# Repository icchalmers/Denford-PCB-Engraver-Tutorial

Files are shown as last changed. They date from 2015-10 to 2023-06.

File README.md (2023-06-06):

# Denford PCB Engraver Tutorial

This tutorial will lead you through using the [Denford PCB Engraver](https://denford.co.uk/products/pcb-engraver/) to mill a small breakout board for a surface mount ATtiny85. The tutorial was written specifically for the FabLab at the University of Strathclyde, but should be applicable to anyone with a Denford PCB Engraver.

The best way to use the tutorial is in the browser. You can start at the beginning my going to the [Introduction](doc/introduction.md) or use the [Index](doc/index.md) to jump straight to a specific section.

The [latest release](https://github.com/icchalmers/Denford-PCB-Engraver-Tutorial/releases/latest) of the tutorial includes all of the example files and also has a PDF version that is easier for printing.

# Author

This tutorial was written by [Iain Chalmers](https://www.linkedin.com/in/iain-chalmers-0394753b). Any feedback is greatly appreciated and can be submitted by [opening an issue](https://github.com/icchalmers/Denford-PCB-Engraver-Tutorial/issues/new) on GitHub.

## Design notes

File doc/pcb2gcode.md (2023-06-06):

# Turning Gerbers Into GCode

To turn our gerber files into GCode that can be used to drive the engraver, we're going to use [pcb2gcode](https://github.com/pcb2gcode/pcb2gcode) with its graphical wrapper [pcb2gcodeGUI](https://github.com/pcb2gcode/pcb2gcodeGUI). In the FabLab@Strathclyde, this should be installed on Laptop 1 in `C:\pcb2gcode`.

When your first open the program, you need to import the settings for the Denford. To do this, go to `File->Load configuration file` and choose the [Denford_pcb2gcode.settings](/Denford_pcb2gcode.settings) file included with this tutorial. Note that this assumes you are using a 0.2 mm, 60° mill for the traces and a 2 mm corncob mill for the board outline. See the [Drill](./pcb2gcode.md#drill) section below for how to change these settings.

In the `Input/output` tab, select the gerbers you generated in the previous step. If you used the default KiCAD naming, your `Front` will be the file that ends in `-F_Cu.gbr`, `Outline` will be the file that ends in `-Edge_Cuts.gbr` and the `Drill` file will end in `.drl`.

One you have these files selected you should get a preview of the PCB as shown below.

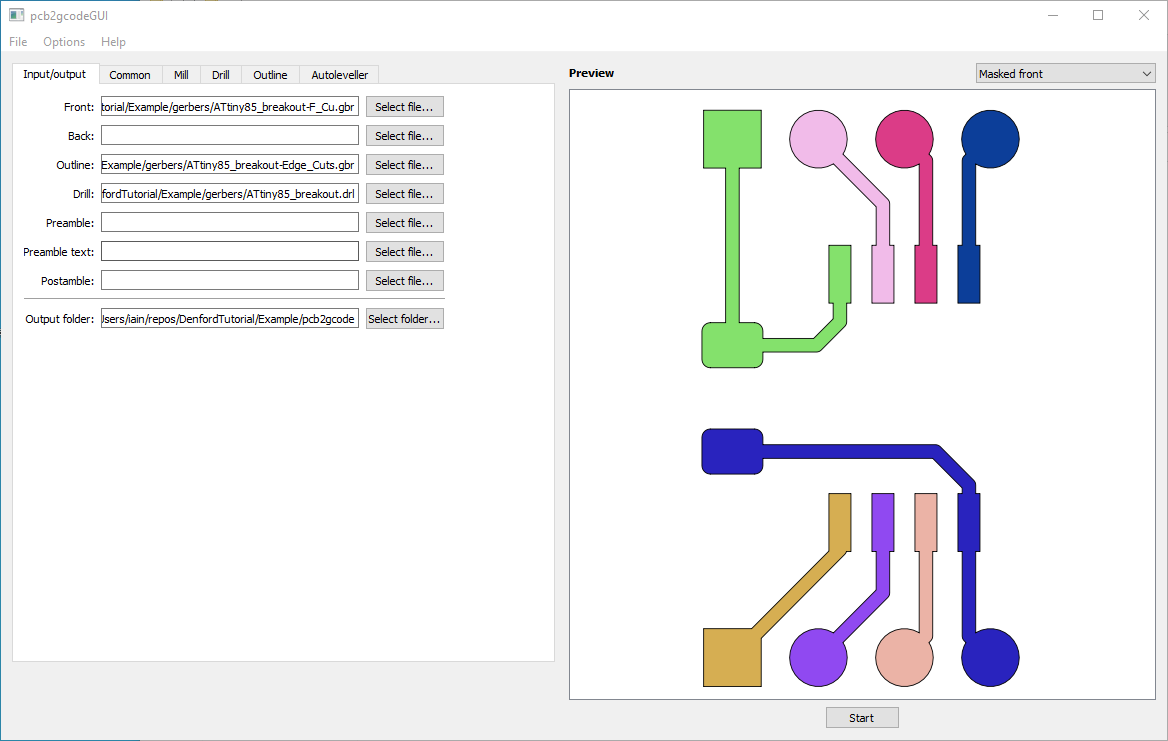
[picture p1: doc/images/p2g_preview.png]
p2g_preview


Once you choose a directory for the output files, you should just be able to hit `Start`. Assuming your design doesn't have any problems, you should see output similar to the below.

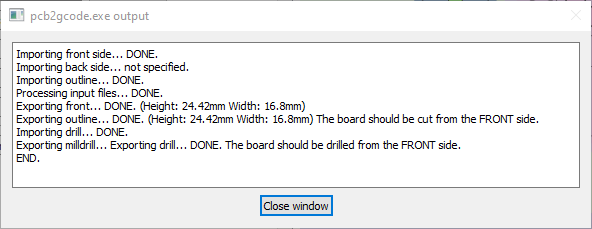
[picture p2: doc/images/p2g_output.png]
p2g_output


The preview window will now update to show the processed front. If there were any problems in the output generation, the preview can help you identify them. Note that where there is insufficient clearance between traces, pcb2gcdoe will default to trying to mill between the traces. This can lead to your traces being too thin, so it's better to fix problems in the design.

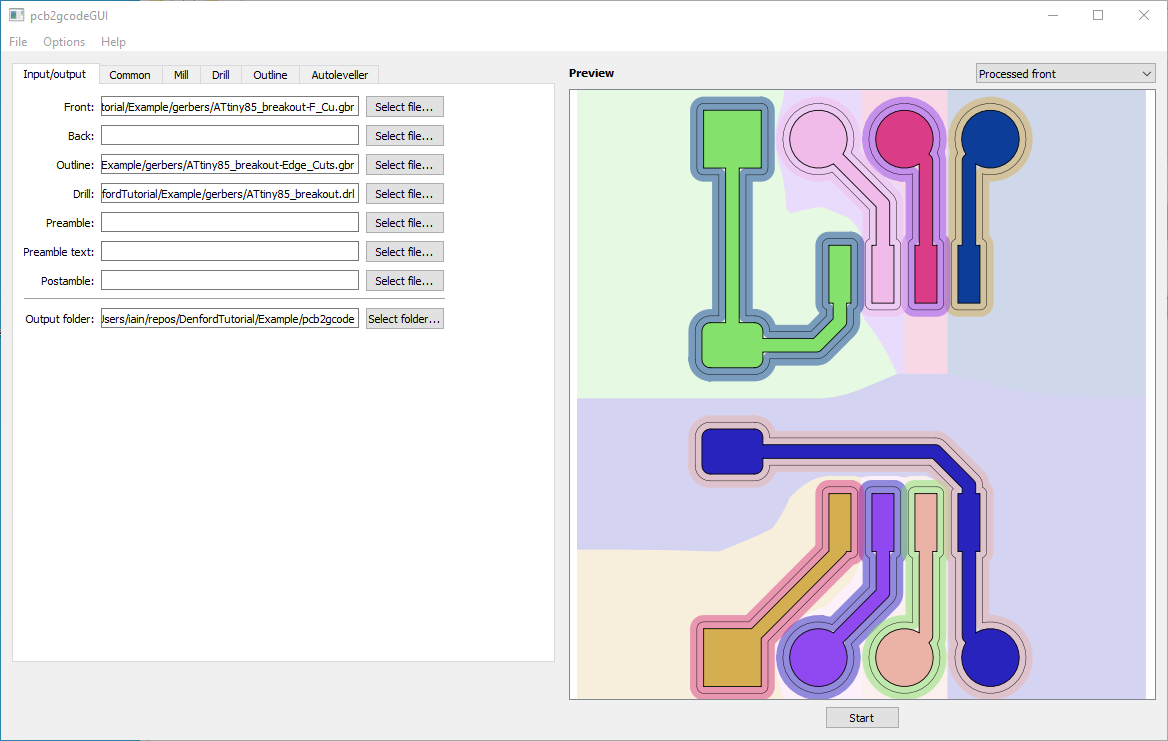
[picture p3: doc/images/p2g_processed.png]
p2g_processed


The output directory should now have a list of files similar to the one shown below. The three files we are most insterested in are the `.ngc` files, as these contain the GCode we will use to drive the Denford.

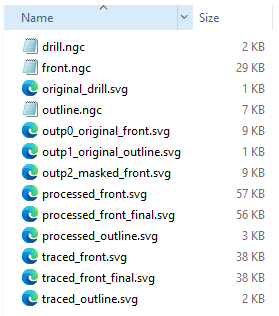
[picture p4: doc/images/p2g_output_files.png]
p2g_output_files


## Manual pcb2gcode Settings

### Common

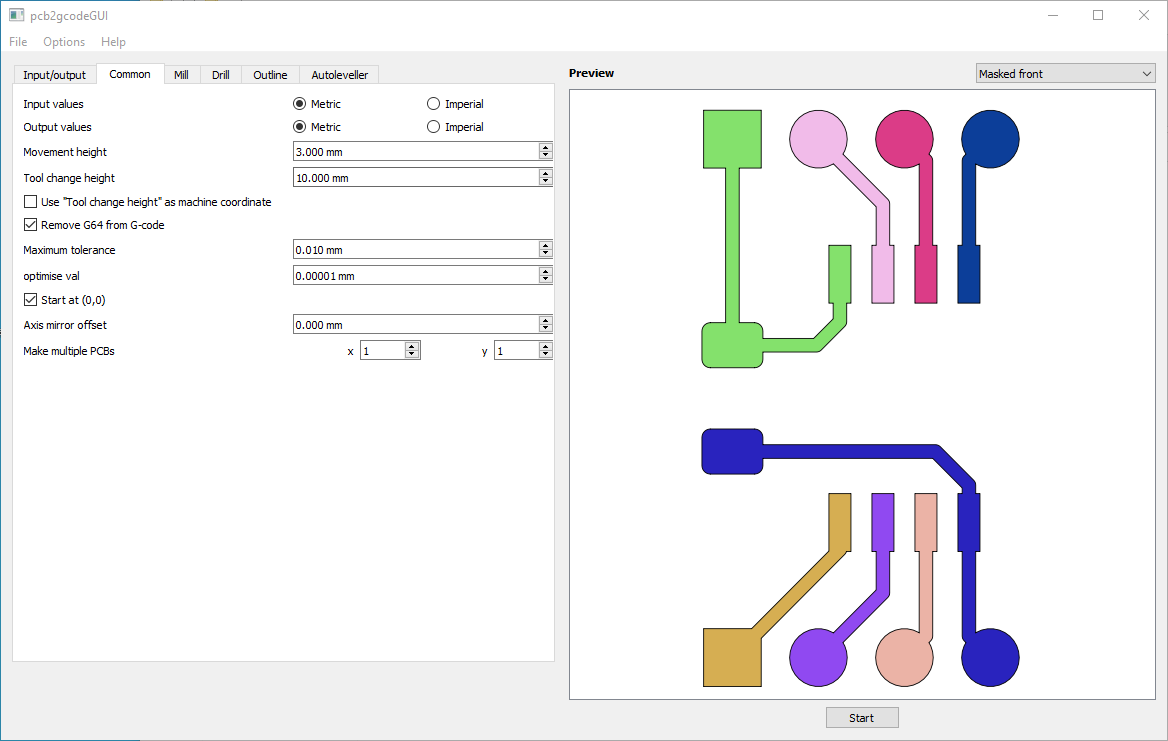
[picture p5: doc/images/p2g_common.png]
p2g_common


### Mill

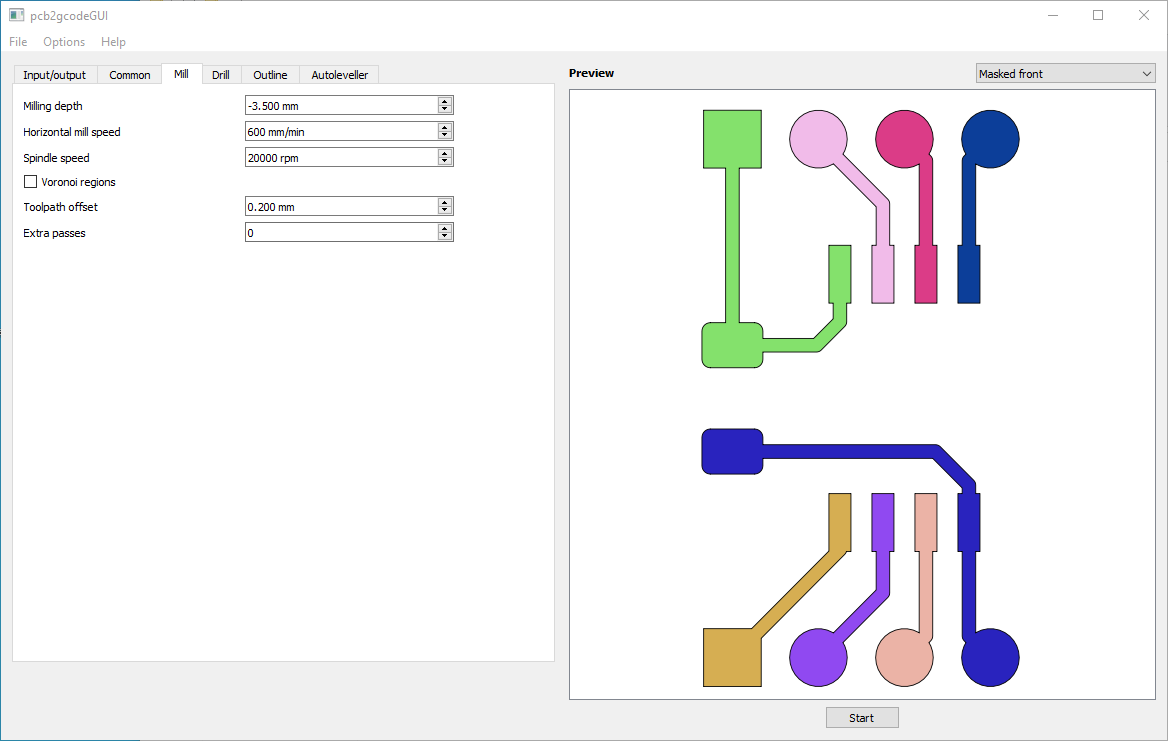
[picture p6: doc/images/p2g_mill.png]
p2g_mill


### Drill

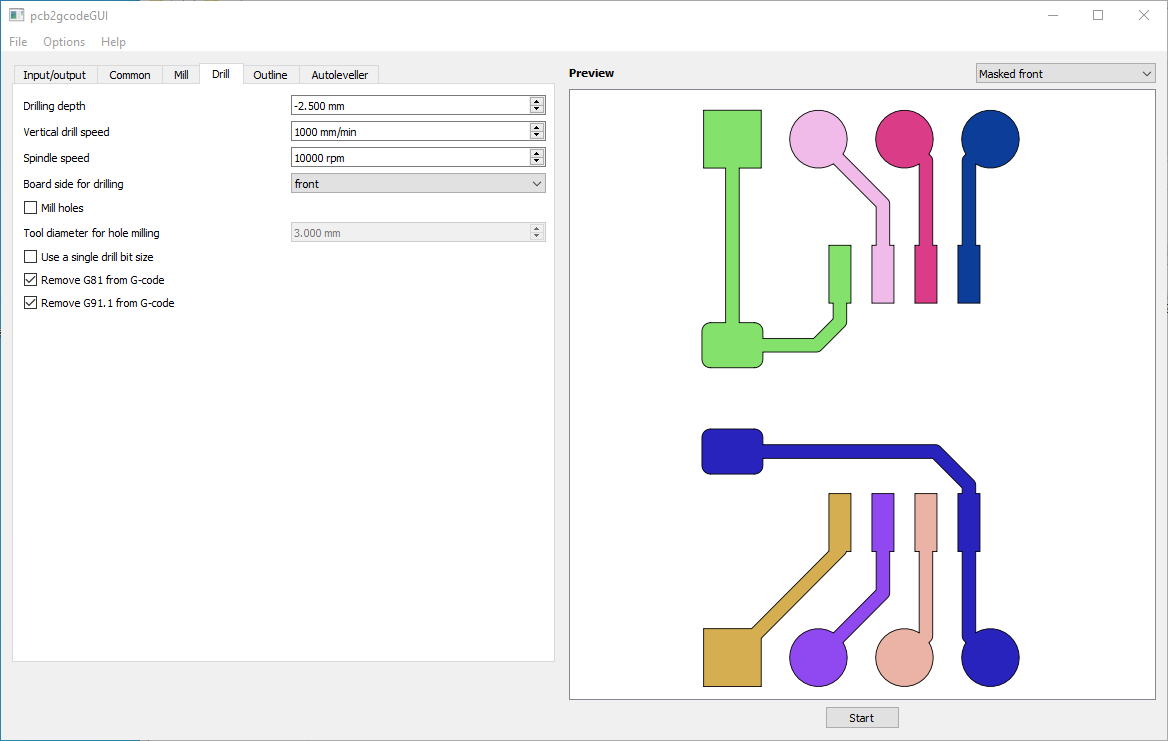
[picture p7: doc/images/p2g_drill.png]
p2g_drill


### Outline

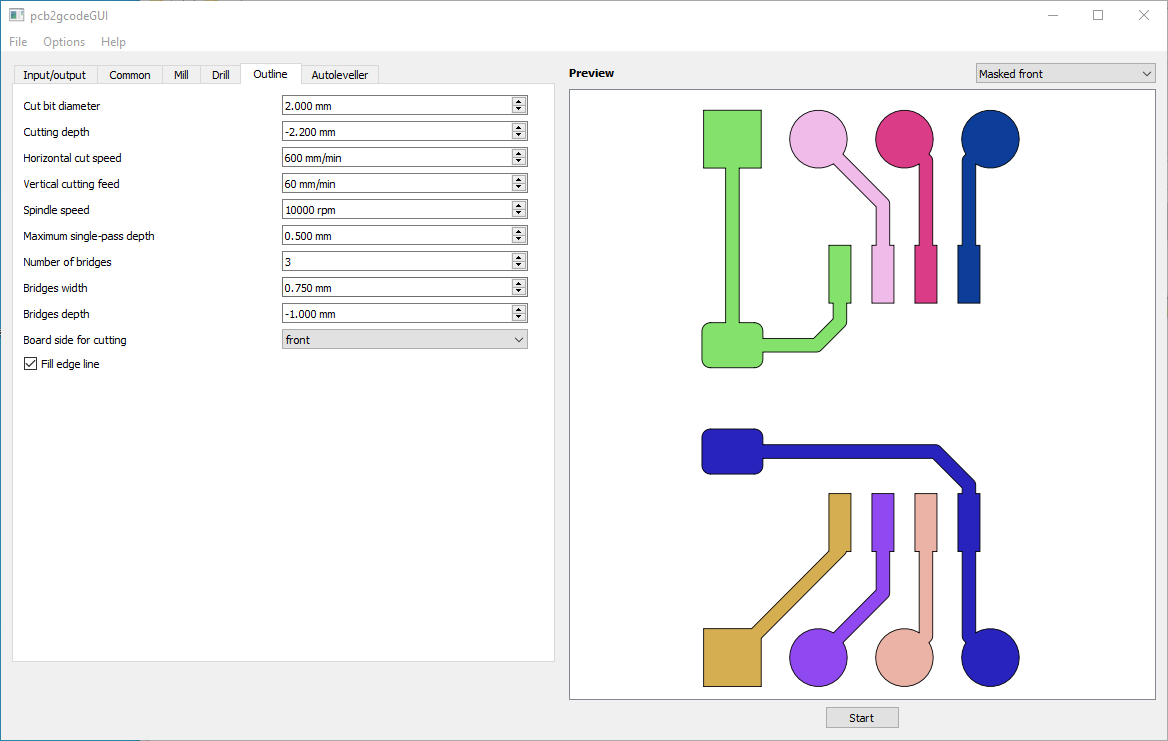
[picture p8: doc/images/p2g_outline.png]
p2g_outline


___
  <[Previous](kicadgerbers.md) | [Index](index.md) | [Next](milling.md)>

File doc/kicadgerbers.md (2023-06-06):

# Generating Gerbers Using KiCAD

In this tutorial, we're going to make a simple breakout board for an ATtiny85. You can find the KiCAD project [here](/example/PCB/).

If you want to skip this step because you don't have KiCAD installed, you can find the generated gerbers files [here](/example/gerbers/).

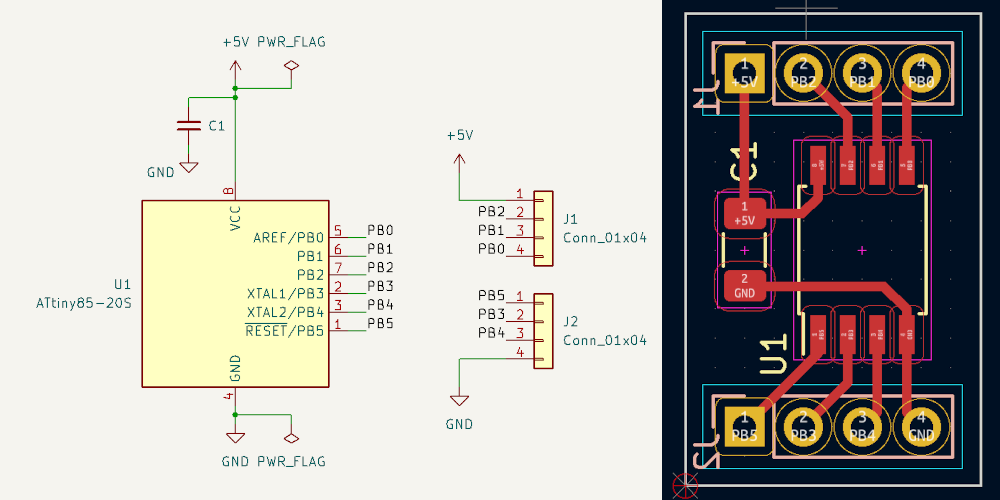
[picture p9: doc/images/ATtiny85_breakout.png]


If you're using different PCB design software, you can probably adapt the settings below for your software. If you want to contribute settings for your software, pull requests are welcome!

## DRC Constraints

Below are the DRC rules we recommend for projects designed to be made on the Denford. If you're using your own design, you can import the design rules from the example project to save yourself some time.

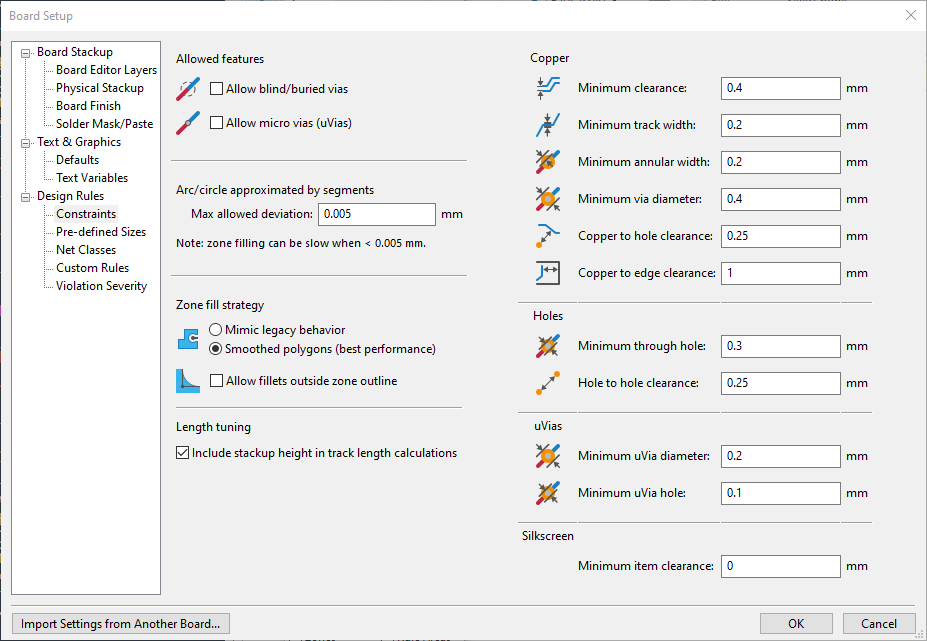
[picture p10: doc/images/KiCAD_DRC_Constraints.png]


## Gerber Generation Settings

Below are the recommended gerber generation settings for gettings gerbers compatible with pcb2gcode. Remember to set a sensible drill/place origin in your design.

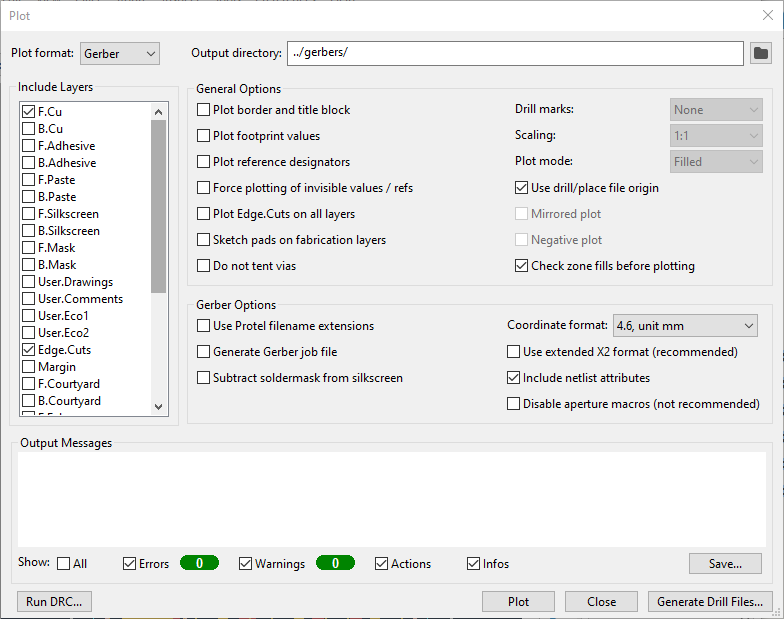
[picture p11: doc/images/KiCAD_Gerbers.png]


For the drill file, it's best to combine all of the drill hits into one file (as we can't do plated through holes anyway).

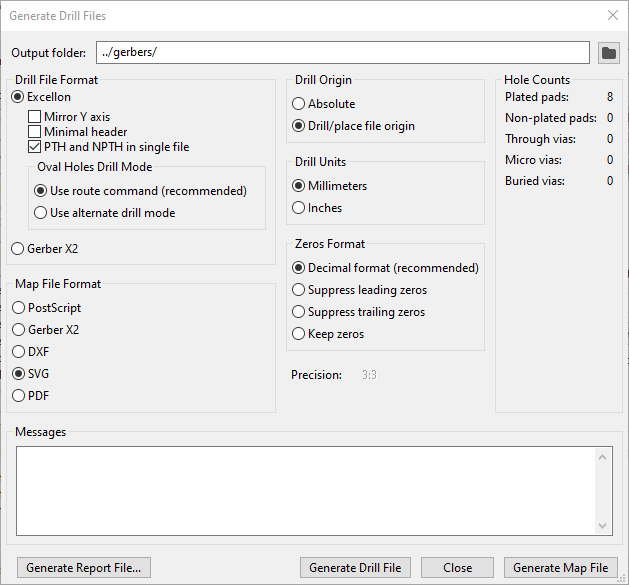
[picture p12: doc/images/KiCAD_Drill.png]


Once your gerber files are generated, you should have a set of files similar to the example ones [here](/example/gerbers/). The next step is to use pcb2gcode to convert our gerber files into GCode that we can use to drive the Denford.
___
  <[Previous](denfordengraver.md) | [Index](index.md) | [Next](pcb2gcode.md)>

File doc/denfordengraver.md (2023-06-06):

# Denford PCB Engraver

## Overview

You can find the full specification for the engraver on the [Denford website](https://denford.co.uk/products/pcb-engraver/). For our purposes, only two of the features are worth discussing:

- The maximum board size is 360 mm x 210 mm.
- The Z axis (that is, the bit that goes up and down) "floats" on top of the workpiece. The big advantage this brings over a traditional CNC is that the depth of cut into the copper (which is only 0.035 mm think) doesn't rely so heavily on the workpiece being completely flat with respect to the machine. That means it's easier to setup and V-shaped cutting bits give more consistent cut widths.

## Capabilities

In the FabLab@Stratchlyde, we use a combination of V-shaped milling bits for milling trace outlines and corncob bits for milling the PCB contour. If you use different bits, you might have slightly different capabilities but the list below should give you a decent idea of what the machine can do.

- **Single Sided PCBs:** While it is possible to engrave double-sided PCBs, it's almost always more hassle than it's worth. You would be surprised how complex a board you can get with just a single layer PCB. What I would call 1.5 layer PCBs are also easy - single layer boards where you add either 0 ohm resistors or a flying wire to jump signals where you need them. If you're feeling masochistic, you can see an example of a double-sided PCB [here](http://fabacademy.org/archives/2015/eu/students/chalmers.iain/week-11-outputs.html).
- **0.4 mm space:** We typically use [0.2 mm, 60° V-bit engraving bits](https://www.shop-apt.co.uk/carbide-engraving-tools-flat-bottom-half-round-60/3-175mm-1-8-diameter-carbide-engraving-cutter-0-2mm-tip-half-round-60.html). By the time these are cutting through the copper we find that they have a cut width of about 0.4 mm. We do have a combination of 0.1/0.2 mm and 30/60° bits, but the 0.2@60° bits are a good compromise between detail and bit life. Smaller spaces are possible with the 0.1 mm 30° bits but they are very fragile.
- **0.4 mm trace:** The hard limit on trace width is actually a fair bit smaller than 0.4 mm (limited by how small you can go before the trace gets lifted in the milling process). From experience, we've found that 0.4 mm for trace/space is a nice combination as it makes it easier to identify when the bits are wearing out, and at that combination you can still sneak a trace between the pads on 1206 (3216M) SMD parts.
- **Contour milling:** This was one of the main drivers to ditch the Denford software for generating the GCode, as it didn't support milling board outlines. pcb2gcode supports complex board outlines and automatically handles things like multi-pass cuts and bridge tabs. We use [2 mm corncob bits](https://www.aliexpress.com/item/32677591025.html?) because they're cheap and pretty hard to break. They don't give the cleanest of cut though, so it's best to keep traces at least 1 mm away from the edge of the PCB. We've experimented with some [2mm endmills](https://uk.rs-online.com/web/p/end-mills/6666681) that gave an excellent finish, but they're not really designed to plunge so required some extra steps to use. Plus, they're a lot more expensive.
- **Drill sizes:** The only sure way to know what drill sizes we have available is to check the box, but 0.5/0.8/1.0 mm are typically safe bets. We do have a range from 0.3 mm to 3 mm but it depends who's broken what recently! Generally it's best to limit yourself to as few drill sizes as possible so you don't have to change the bit a million times. I personally find you can bodge most drill hits to 0.5 mm for through hole components, 1 mm for headers and 3 mm for mounting holes.

## Limitations

Aside from the above, there are a few specific limitations that are worth keeping in mind:

- **FR1/FR2 substrates:** This is the copper clad material we mill the PCB from. We only allow the use of FR1 or FR2 substrates on the engraver.
  - FR1 is ideal as it is easy to mill. The downside is that it's a nightmare to source in small quantities at a reasonable price. We also found that it wasn't suitable to use in the reflow oven as the substrate tended to start to burn.
  - FR2 is a bit tougher on the bits but more widely available. Most of the PCB blanks we have in the FabLab@Strathclyde are FR2
  - FR4 is **not allowed** to be used in the engraver. Not only is the dust toxic, but FR4 is much harder than FR1/FR2 and it significantly reduces the life of the milling bits.

  To enforce this, **only materials purchased from the FabLab can be used on the engraver.** The main downside of FR2 is that it isn't capable of handling as high temperatures as FR4. It is possible to use it in the reflow oven, but it doesn't leave the best finish.
- **No solder mask:** Solder mask is the green stuff on top of almost every PCB you see. It protects the raw copper and also helps during soldering by forcing the solder to go where it's meant to. Without a solder mask, you can still use the reflow oven but it has a tendency to heavily discolour the copper to the point it looks burnt.
- **No silkscreen:** The lack of silkscreen can be unexpectedly annoying when it comes to populating your PCB!

## When To Use The Denford PCB Engraver

Keeping in mind the above capabilites and limitations, here's some advice on when the Denford PCB Engraver is a good choice for making your PCB:

- Simple quick'n'dirty prototypes. If you just need to prove out an idea, you can iterate on multiple designs in a day.
- If you need a breakout board for an IC because you forgot to order adapters.
- For one-off designs. For example, if you need to get a bunch of LEDs in the right place in a 3D model and you need a weird PCB shape to make it work.

I wouldn't recommend the engraver if:

- You want multiple copies of a finalised design.
- You want a long term, high quality PCB.
- Your design isn't simple enough to be implemented on a single layer PCB. The more complex a PCB (in terms of size, part and trace count), the more likely you are to run into issues producing it.

Once you're happy that your design is compatible with the engraver, it's time to generate the gerber files.
___
  <[Previous](introduction.md) | [Index](index.md) | [Next](kicadgerbers.md)>

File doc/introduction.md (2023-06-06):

# Introduction

This tutorial will lead you through using the [Denford PCB Engraver](https://denford.co.uk/products/pcb-engraver/) to mill a small breakout board for a surface mount ATtiny85. The tutorial was written specifically for the FabLab at the University of Strathclyde, but should be applicable to anyone with a Denford PCB Engraver.

If you are in the FabLab@Strathclyde, you should use this tutorial as a supplement to your machine induction.

All the files for this tutorial can be found on github: <https://github.com/icchalmers/Denford-PCB-Engraver-Tutorial>

Any feedback is greatly appreciated and can be submitted by [opening an issue](https://github.com/icchalmers/Denford-PCB-Engraver-Tutorial/issues/new) on GitHub.

## Prerequisites

This tutorial assumes you already know how to design a PCB in your CAD software of choice and generate gerber files for fabrication. The tutorial does cover how to generate gerbers suitable for the engraver using KiCAD, but the general settings should be easy enough to translate to other software (Eagle, Altium etc).

If you don't know how to design a PCB yet, I would recommend looking at [KiCAD](https://www.kicad.org/). Here are a few recommended resources to get your started:

- The KiCAD website has a (small) list of [recommended resources](https://www.kicad.org/help/learning-resources/).
  - In particular, see the offical KiCAD [Getting Started](https://docs.kicad.org/#_getting_started) guide.
- Chris Gammel of [Contextual Electronics](https://contextualelectronics.com/) has two excellent free course that teach you how to design a simple PCB:
  - [Shine On You Crazy KiCAD](https://contextualelectronics.com/courses/shine-on-you-crazy-kicad/)
  - [Getting to Blinky 5.0](https://contextualelectronics.com/courses/getting-to-blinky-5-0/)

## Software

To produce our PCB we'll be using two main pieces of software:

- [Denford PCB Engraver V1.9](https://denford.co.uk/software-downloads-support/): Although this is available for download on the Denford website, it needs a licence to work. It is only used for controlling the engraver, so you can still prepare all your files without it. If you're in the FabLab@Strathclyde, it should already be installed on Laptop 1.
Technically, the Denford software is capable of generating the milling files from gerbers directly, but it's very buggy and lacks some key features.
- [pcb2gcode](https://github.com/pcb2gcode/pcb2gcode): This is the software we use to turn gerbers into gcode that can be used on the engraver. Technically, we're using two bits of software. pcb2gcode is a command line only piece of software for turning gerber files into gcode for milling. We'll also be using the [pcb2gcodeGUI](https://github.com/pcb2gcode/pcb2gcodeGUI) wrapper to add a more user friendly interface and visualise the output. If you're in the FabLab@Strathclyde, it should be installed on Laptop 1. If there is no shortcut on the desktop, you can find it in `C:\pcb2gcode`.
  - When writing this tutorial I used pcb2gcode v2.5.0 and pcb2gcodeGUI v1.3.2-1. Installing these on Linux is pretty easy, but for Windows it can be a bit of a nightmare. I've included pre-compiled x64 Windows binaries in the [releases](https://github.com/icchalmers/Denford-PCB-Engraver-Tutorial/releases/latest) of this tutorial. See the readme in the release for installation help.
- [KiCAD](https://www.kicad.org/) (optional): I use KiCAD as my PCB design software and this tutorial will cover generating gerber files suitable for the engraver using KiCAD, but you can skip this if you already have gerbers ready to use. The [example PCB](/example/PCB/) was created in KiCAD V6.0.

Before we get started, we'll take a quick look at the Denford PCB engraver, it's capabilities and some things to keep in mind when designing circuits to be milled on it.
___
  <[Previous](index.md) | [Index](index.md) | [Next](denfordengraver.md)>

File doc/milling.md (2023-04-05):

# Milling With The Denford PCB Engraver

___
  <[Previous](pcb2gcode.md) | [Index](index.md)>

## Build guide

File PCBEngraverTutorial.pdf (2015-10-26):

### Denford PCB Engraver Tutorial Denford PCB Engraver Tutorial

This tutorial will lead you through using the Denford PCB Engraver to mill a small breakout board for a surface mount ATtiny85. The board was designed in KiCAD.

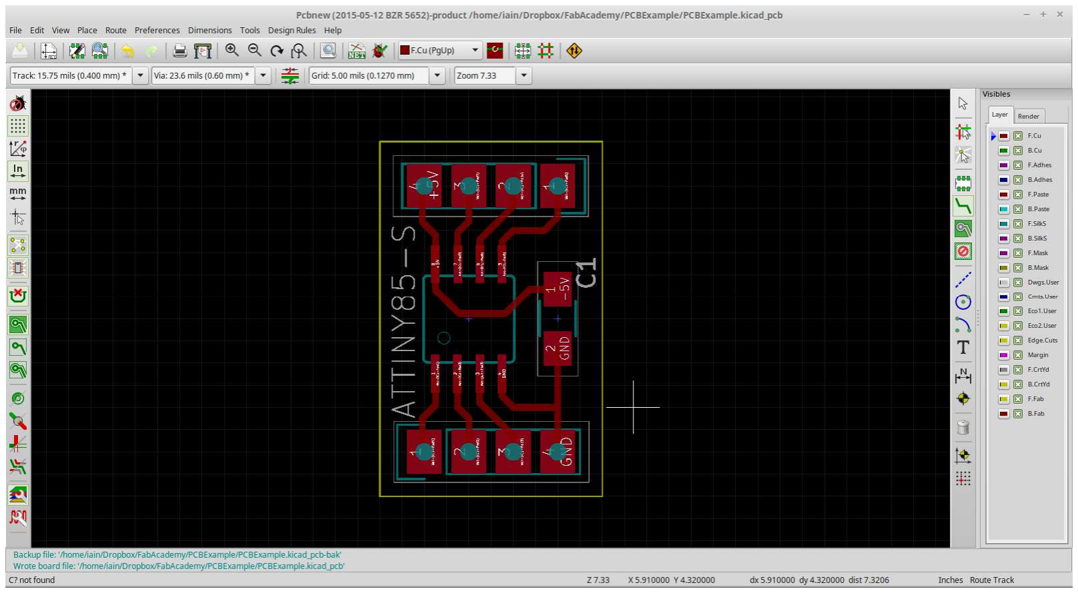
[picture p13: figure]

All the files for this tutorial can be found on my github: https://github.com/icchalmers/Denford-PCB-Engraver-Tutorial

Some points to remember before we get started:
- Think “Design For Manufacture”.
- Endmills are 0.4mm.
| Minimum distance between your traces should be 0.4mm.
| I use a default trace width of 0.4mm in my designs too. • Helps identify old endmills.
| • Big enough traces that they are less likely to rip up.
- 1206 SMD (surface mount) components are a good standard (and the size we stock in the FabLab).
| Big enough to solder “easily”.
| Can fit a trace between the pads.
- EACH ENDMILL COSTS OVER £10!
- They are VERY easy to break, so take care!
- Single sided boards are best.
- You would be surprised how complex a design can get before you really need double sided boards.
- Double sided is possible but fiddly to align and get right, take ages to do and even longer to solder (because you need to solder wire in your vias).

- Best option is to do as much on a single side as you can, and then either use 0Ω resistors or pieces of wires to make any necessary jumps.
- Automatic drilling of through holes.
- But try keep to SMD parts if you can. It’s easier, faster and components tend to be cheaper.
- Pin headers are a good except to this – they benefit from the extra mechanical security of through hole compared to surface mount. It helps stop you ripping up traces if you are plugging/unplugging things a lot.
- Use FR1 copper clad board. It gives the best cut and has the least wear on the endmills.
- FR2 is OK. Most of the stock in the lab is FR2 purely because it is easier to source.
- DO NOT USE FR4! It wears out the endmills because it is so hard, and the dust is TOXIC.
- Basically, only use copper clad board supplied by the FabLab…

### Loading The Design Loading The Design

Turn on machine (red switch on the side) and plug it into the laptop. (Not all laptops have the software, check the chart on wall).

Open PCB Engraver software. The icon is on the desktop.

You software will load the FLASH of the PCB engraver, and you will be presented with the default screen.

- If you opened the software before turning on/connecting the machine, you will need to hit

the Connect button.

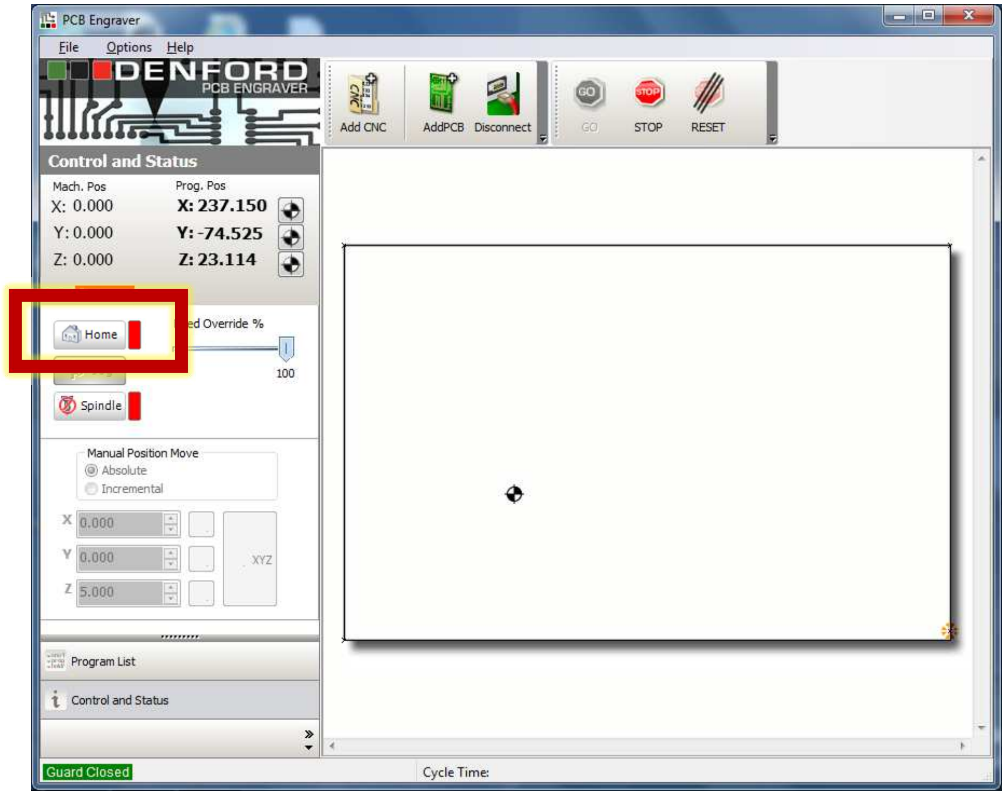
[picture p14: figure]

Make sure the machine lid is closed and click the Home button.

Notice that the other options are now enabled.

Click AddPCB button.

Select the gerber file for your top copper (you might need to enable viewing off all file types, depending on the file extension of your gerbers).

The PCB Manufacture Wizard will open.

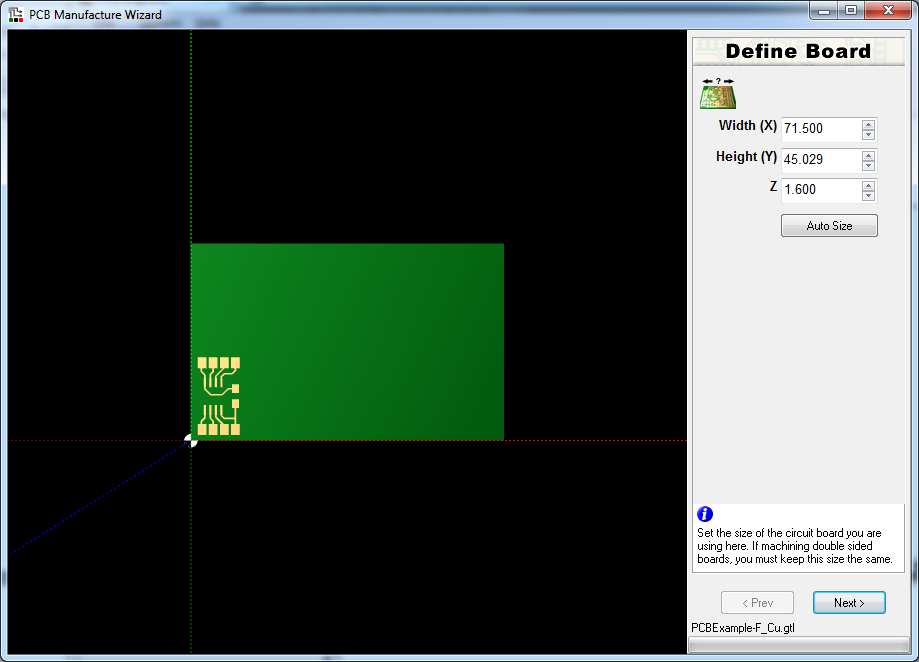
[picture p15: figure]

Check that your design looks OK.

- One error I have seen is that hexagonal pads exported from Eagle sometimes don’t import

properly (change them to be circles as a workaround if you have this problem).

Hit Auto Size. This doesn’t actually affect the final cut, but just makes the view tidy.

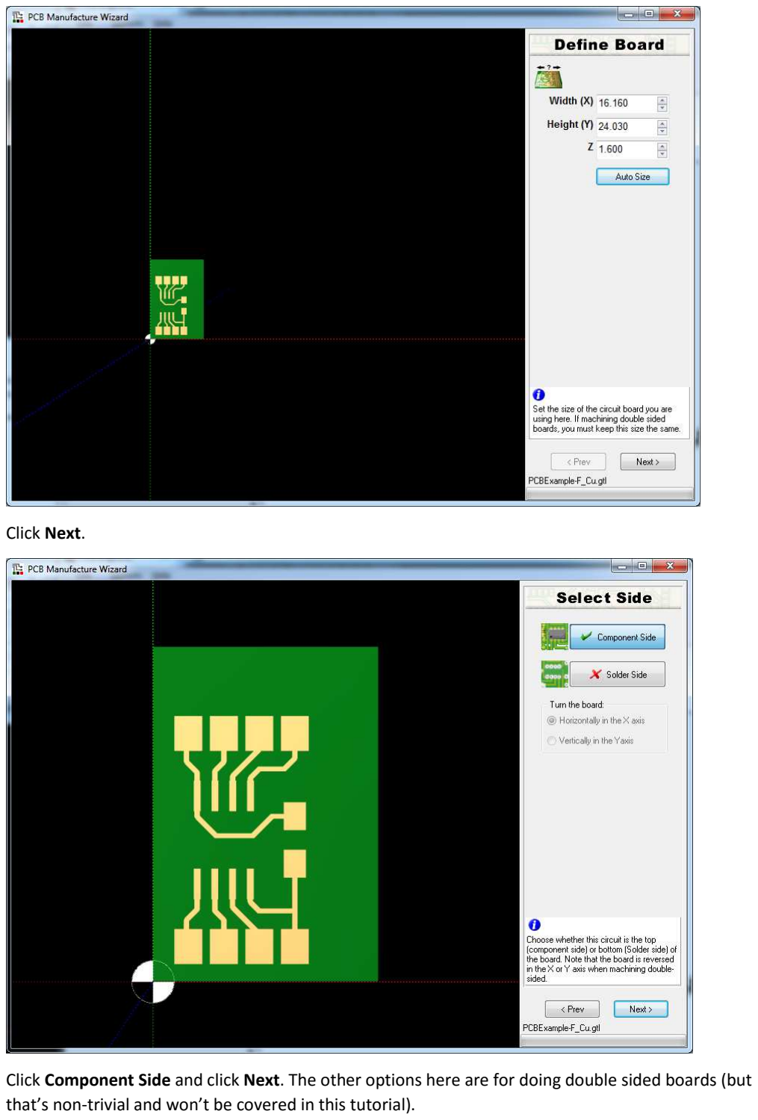
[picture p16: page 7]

Click Next.

Click Component Side and click Next. The other options here are for doing double sided boards (but that’s non-trivial and won’t be covered in this tutorial).

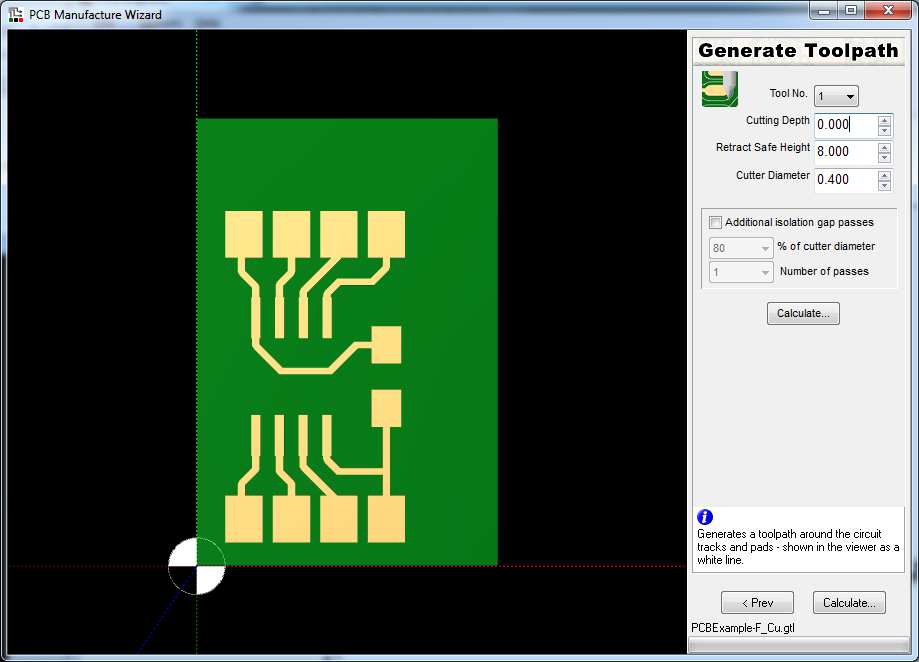
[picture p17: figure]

In this step, we define how we will cut the traces of the PCB. The important parameters are:

- Cutting Depth: This is how deep the PCB engraver will cut. Because we have a floating head,

this setting is largely unnecessary. Set it to 0mm.
- Retract Safe Height: This is a VERY IMPORTANT SETTING! This is how high the drill goes

when moving between cutting the PCB traces. I would highly recommend setting it to AT LEAST 7mm. More on why later.
- Cutter Diameter: This is where we tell the software how big our endmill is. The ones we

have in the lab are 0.4mm

Depending on your design, with the Cutter Diameter set to exactly 0.4mm you might get the following warning when you click Calculate.

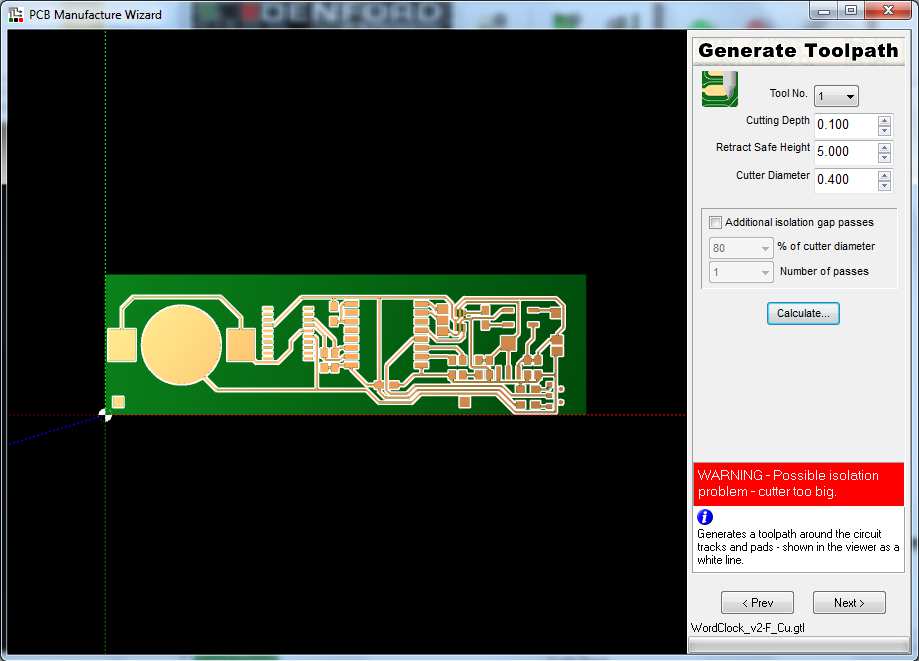
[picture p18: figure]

This basically means that there were parts of your design that the software doesn’t thing it can fit a 0.4mm cutter through. This happens a lot, even if your PCB passed a design rule check for 0.4mm clearance.

Very unhelpfully, the software is rubbish and doesn’t show you where the error has happened. Zoom in and scroll around and look for the problem points. In this more complex PCB design, it’s around a very small footprint shown below.

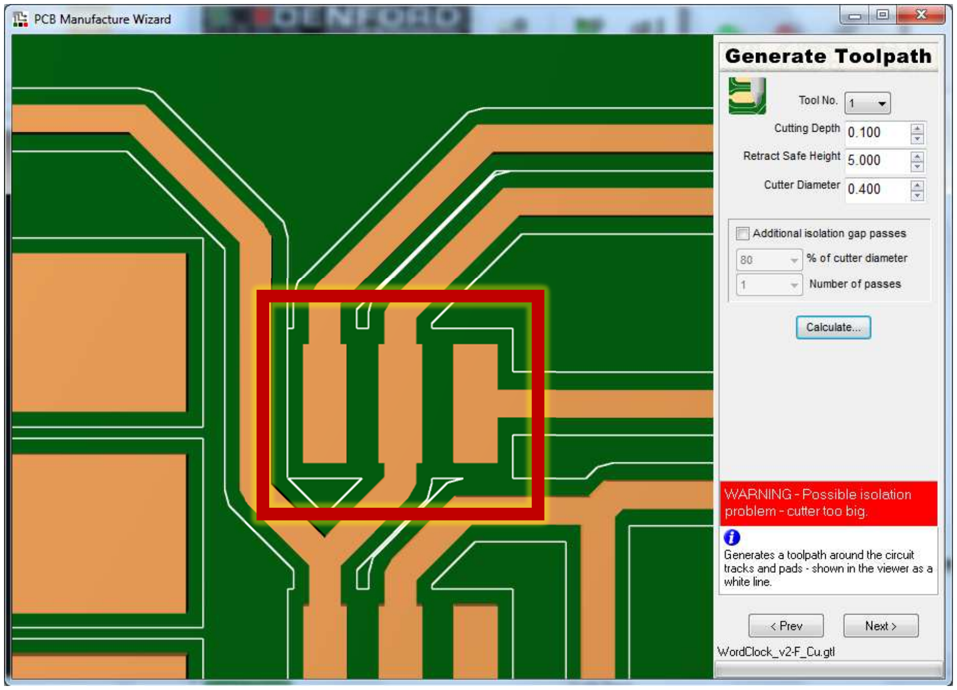
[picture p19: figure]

Notice that the white line (the cutter path) doesn’t go between all of the pads. If we were to cut this design, those pads would still be connected together.

There are two ways to solve this problem:

1. Edit your design to have more clearance between pads/traces.
2. Tell the software your endmill is smaller than it actually is.
- Usually setting the endmill size to 0.39mm will do.

In the case of the PCB shown, setting the endmill size to 0.395mm was enough for the path to be generated without issue. Just be sure to not go too small! For example, telling the software your endmill is 0.2mm will result in you getting super thin traces. I wouldn’t suggest going lower than about 0.35mm – after that, fix your circuit.

For the basic PCB included with this tutorial, the cut path will generate without any warnings. The cut path is displayed as a white line around the PCB traces.

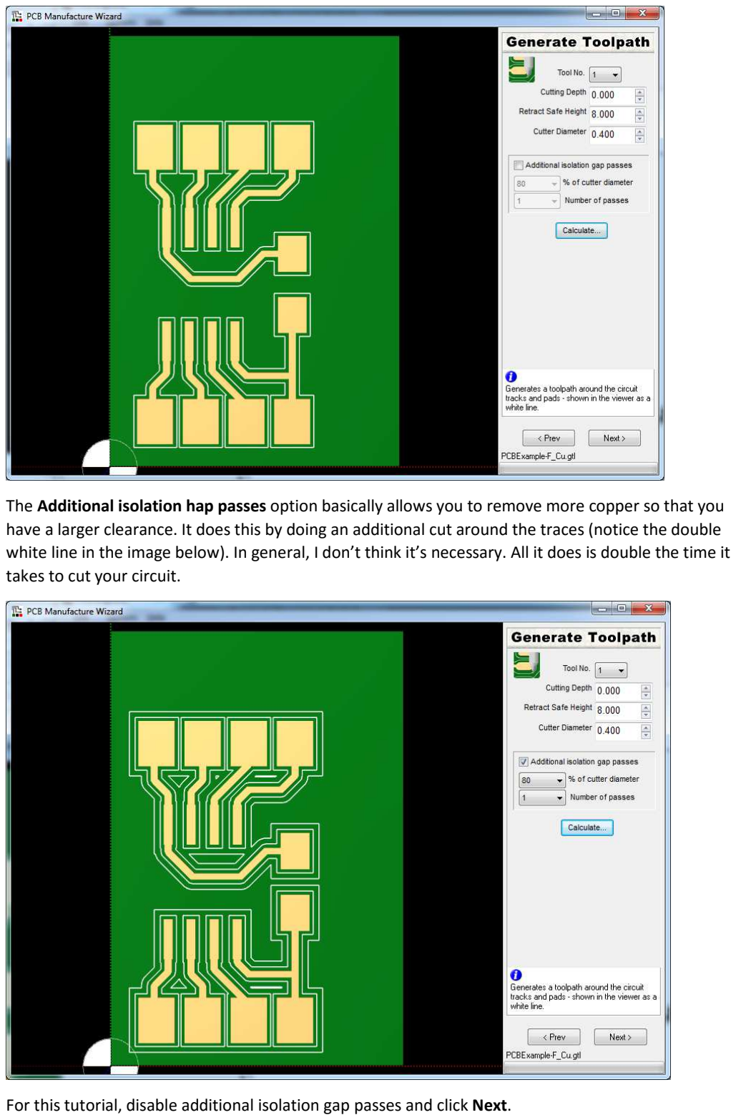
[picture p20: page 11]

The Additional isolation hap passes option basically allows you to remove more copper so that you have a larger clearance. It does this by doing an additional cut around the traces (notice the double white line in the image below). In general, I don’t think it’s necessary. All it does is double the time it takes to cut your circuit.

For this tutorial, disable additional isolation gap passes and click Next.

This screen allows you to define your drilling operation.

Getting the Denford software to accept your drill file can be a bit of a black art. An EXCELLON drill file generated from Eagle using the SparkFun CAM file tends to import OK (although the drill sizes will be meaningless). From KiCAD, I’ve found that you need to hand edit the drill file to add three zeros to the end of each coordinate. Compare the drill files PCBExample_original.drl and PCBExample_fixed.drl for an example of the edits you might need to make.

Don’t bother with the Auto Drill option – it doesn’t do anything…

If you import a drill file and you only get yellow markers around the origin like in the image below, you know you have a problem with the file format.

Assuming your file imports OK, you should see yellow markers showing your drill hits.

The import settings are:

- Drilling Depth: This is a VERY IMPORTANT SETTING! It might seem counter intuitive, but you

should set the drill depth to 0. We will be using the floating head on the PCB engraver to control the drill depth.
- Pilot Drill Only: If you have this box checked, then all your drill hits will be done using the

same drill bit. If you uncheck this box, the machine will ask you to change the drill but for every different hole size. Notice that the drill size never seems to import properly: in the image above, the holes were 1 mm. Instead, make a note of which tool number matches to which holes and make sure you use the right drill bit later.

Click Next.

THIS IS THE MOST MISLEADING AND USELESS PART OF THE SOFTWARE.

The settings on this page actually have NO relation to how fast the machine will actually travel! We broke a lot of bits before we figured that out…

So, ignore this page, and just click Next.

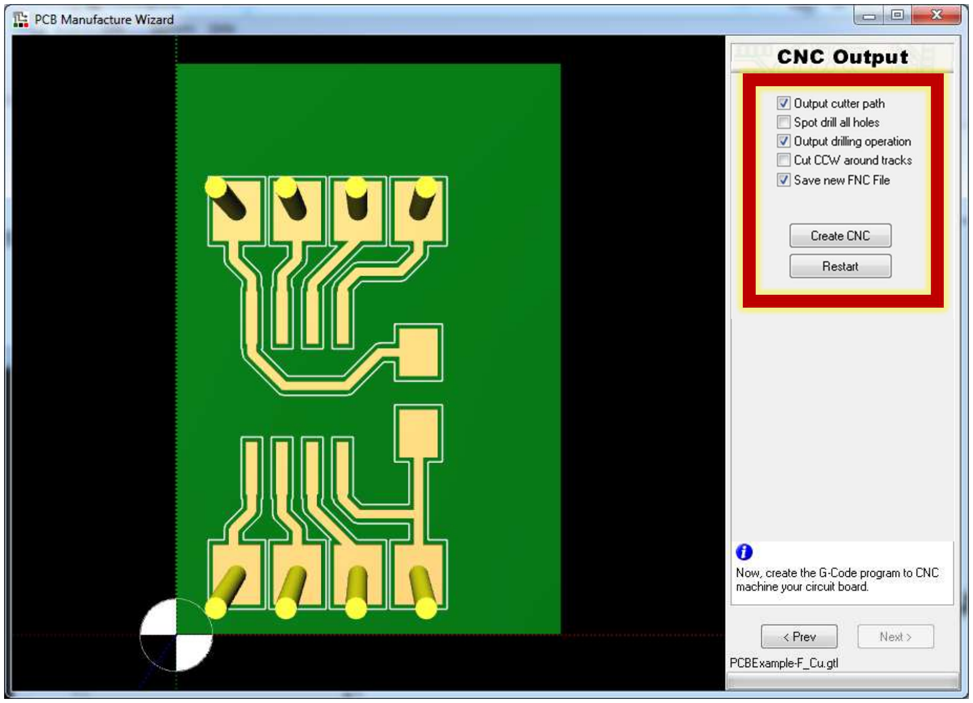
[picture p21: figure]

This is the final step in the wizard. Take a final look at your circuit – this is what will get cut/drilled.

The settings are:

- Output cutter path: This should be CHECKED. This is what actually outputs the trace cutting

path.
- Spot drill all holes: This should be UNCHECKED. If you leave this checked, the final step of

cutting the traces with the 0.4mm bit will be to tap the centre of each drill hole. This is useful if you plan on drilling the holes by hand, but we’re automating that step. Spot drilling just wastes time.
- Output drilling operation: This should be CHECKED. If it’s not, then the machine won’t drill

any of the holes we imported.
- Cut CCW around tracks: This should be UNCHECKED.
- Save new FNC File: This should be CHECKED.

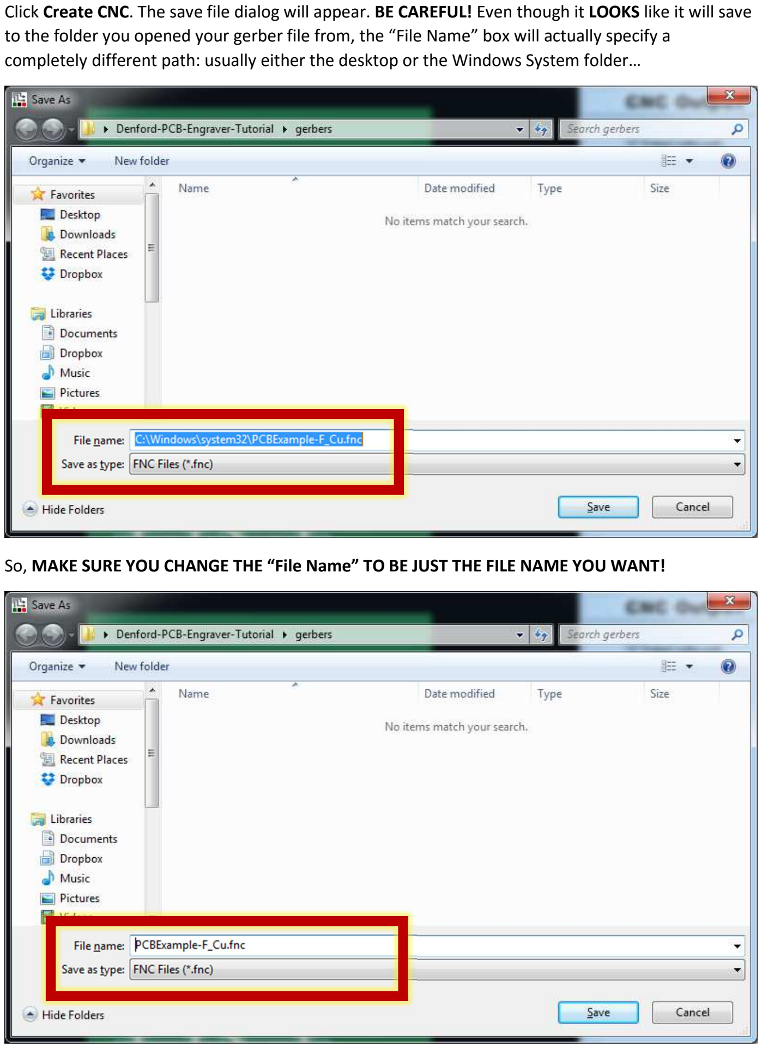
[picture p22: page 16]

Click Create CNC. The save file dialog will appear. BE CAREFUL! Even though it LOOKS like it will save to the folder you opened your gerber file from, the “File Name” box will actually specify a completely different path: usually either the desktop or the Windows System folder…

So, MAKE SURE YOU CHANGE THE “File Name” TO BE JUST THE FILE NAME YOU WANT!

Your PCB will automatically be imported (although you might not be able to see it yet depending on where the current origin is set). The next step is to place our FR1 in the engraver. To make things easy, we’ll reposition the bed to the front of the machine using the Jog option.

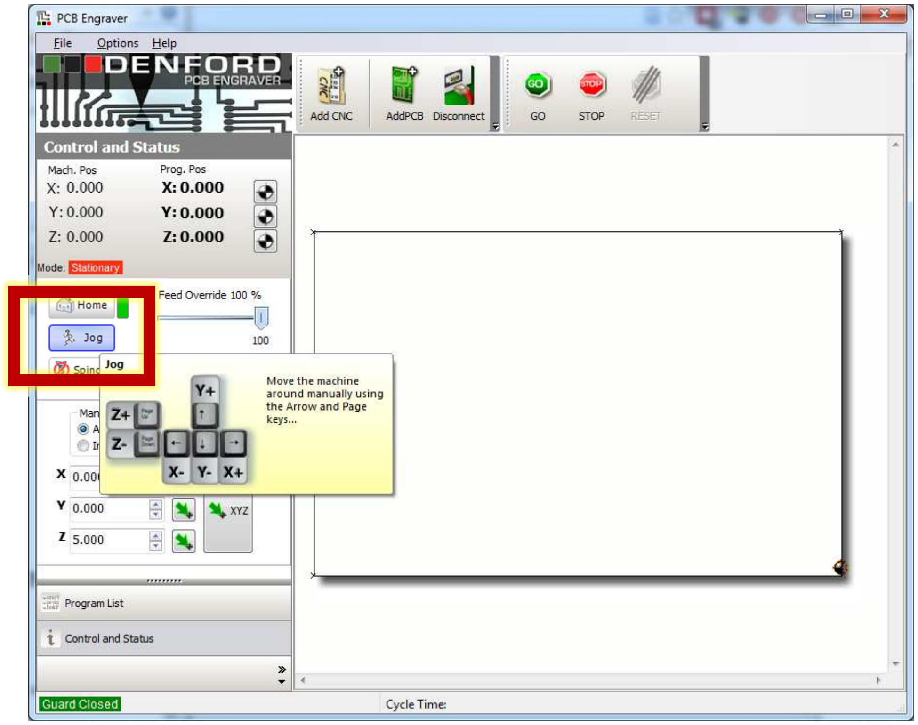
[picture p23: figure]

Click on Jog and use the arrow keys to bring the workbed to the front of the machine.

Notice that we have a sacrificial piece of FR1 already on the machine bed. This is to stop the actual acrylic bed from getting damaged.

When it comes to choosing a piece of FR1 there are two options:

1. Pick a piece a bit bigger than your actual circuit – Graham/Lindsey can cut it to roughly the right size for you using the bandsaw. When you’re finished, just pry it off and either use it as is or ask Graham/Lindsey to trim it down for you. This is the easiest option.
2. Use a piece larger than your circuit, and then cut the circuit out on the machine using a large diameter endmill. This option is harder (it involves hand-editing some G-Code) but gives you more flexibility. For example, you can cut more complex shapes or cut multiple circuits from the same piece of FR1.

In either case, stick your piece of FR1 onto the sacrificial piece using some double sided tape. If your circuit is quite small, you can get away with using the weaker double sided tape (which is good, because it’s easier to take off and to clean!). If you have quite a large piece, use the stronger carpet tape usually used for the CNC machine. The downside is that you’ll need to use some white spirit/acetone to clean it, and probably use the heat gun to get your PCB off the sacrificial layer.

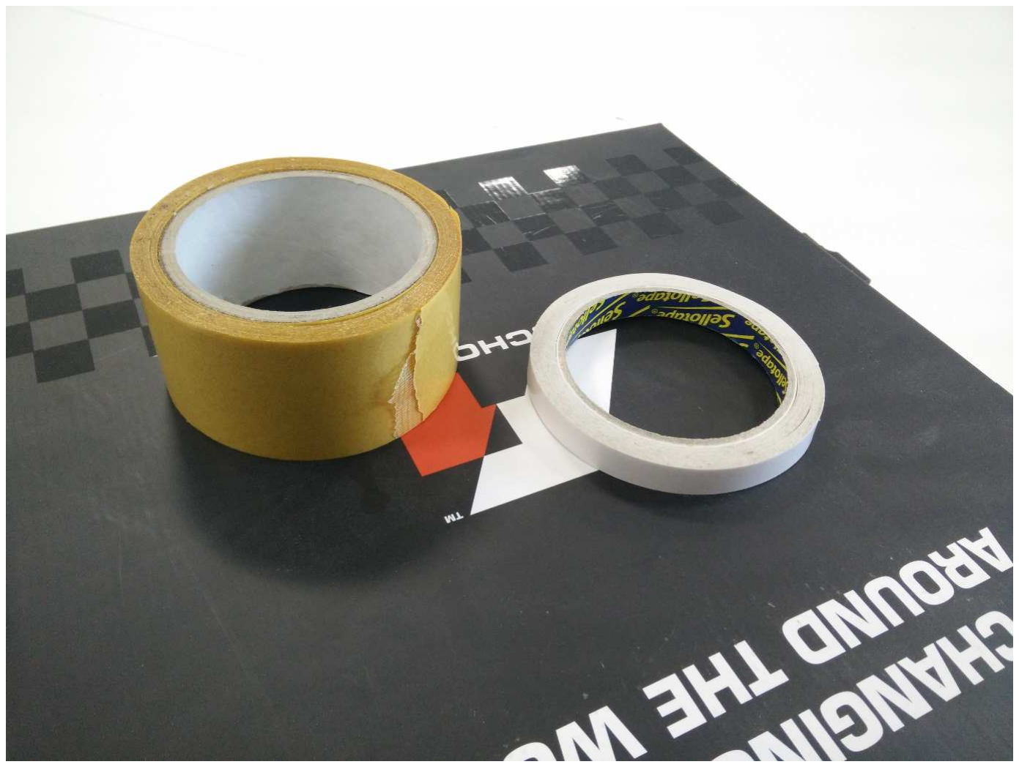
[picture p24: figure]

Try and make sure that the edges of your FR1 are roughly parallel with the edges of the workbed. You should end up with a setup similar to the one shown below.

Now to set the origin, which is the bottom left corner of our PCB. Using the jog setting, move the cutter to roughly the bottom left hand corner of where you want your PCB to be on the FR1.

CHANGE TOOL IF NECESSARY – Check motor ON and at 16k rpm

VERY IMPORTANT! Now, reduce the Feed Override setting to 15%. This will slow the movement speed of the cutter. You can now fine tune the XY origin point of your PCB. You can use the Page

Down and Page Up buttons to move the machine head up and down. BE CAREFUL NOT TO PLUNGE THE ENDMILL INTO THE PCB! You’ll break the endmill if you do.

When you are happy with the XY position, set it as the XY origin by clicking the target symbol next to the X and Y position indicators.

Notice that our PCB has now come into view on the virtual workbed, and that the XY program position of the machine now shows (0, 0). The machine head should now be sitting slightly above your PCB origin point.

Now we need to set the Z height. Start by clicking the Spindle button to turn on the spindle. MAKE SURE YOU TURN ON THE SPINDLE! If you don’t, you’ll break the bit! Also turn on the vacuum – it’s the big red button on the handle. Now using the jog setting, lower the endmill into the FR1 until the white ring is sitting on the copper as shown below.

Once the white ring is touching the copper, zero the Z axis. Now, keeping an eye on the Z position, lower the machine head again until the Z axis reads about -1.5mm. The actual endmill won’t move any deeper into the copper because of the floating head, but will now “float” over the copper and help compensate for any variations in the height of the FR1 relative to the workbed. Now zero the Z axis again.

At this point you might want to retract the endmill out of the copper and check that it left a small drill in the copper, like the one shown below.

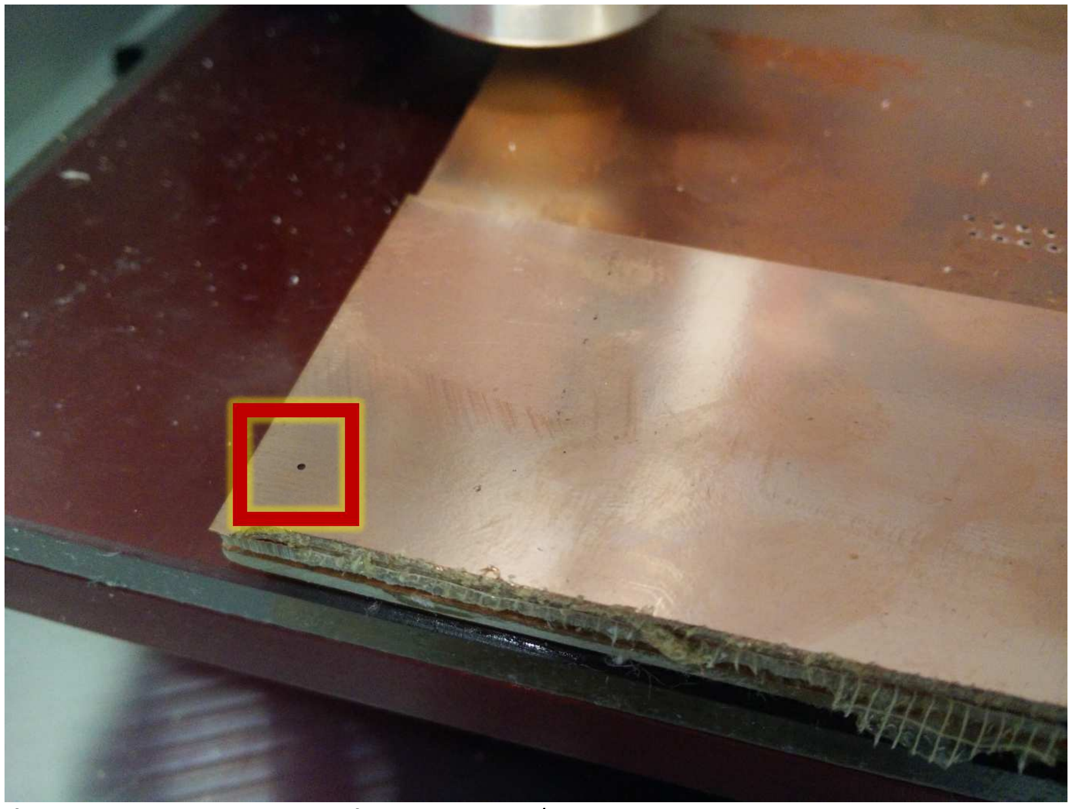
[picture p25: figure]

If you need to adjust the depth of cut, ask Graham/Lindsey. The depth should be set to be just deep enough to reliably cut through the copper without leaving deep grooves on the board.

We’re finally ready to cut the traces of the PCB! Hit the RESET button. CHECK THAT THE FEEDRATE IS SET TO 15%! When you’re ready, turn on the vacuum and press the GO button. Depending on what tool was used last, the software might ask you to change to tool. We’ve already done that, so just click OK.

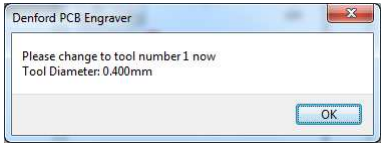
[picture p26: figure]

When the traces are finished cutting (it will take about three minutes for this simple circuit), the machine will ask you to change the tool to drill the holes. If everything is going to plan, your traces should look something like this

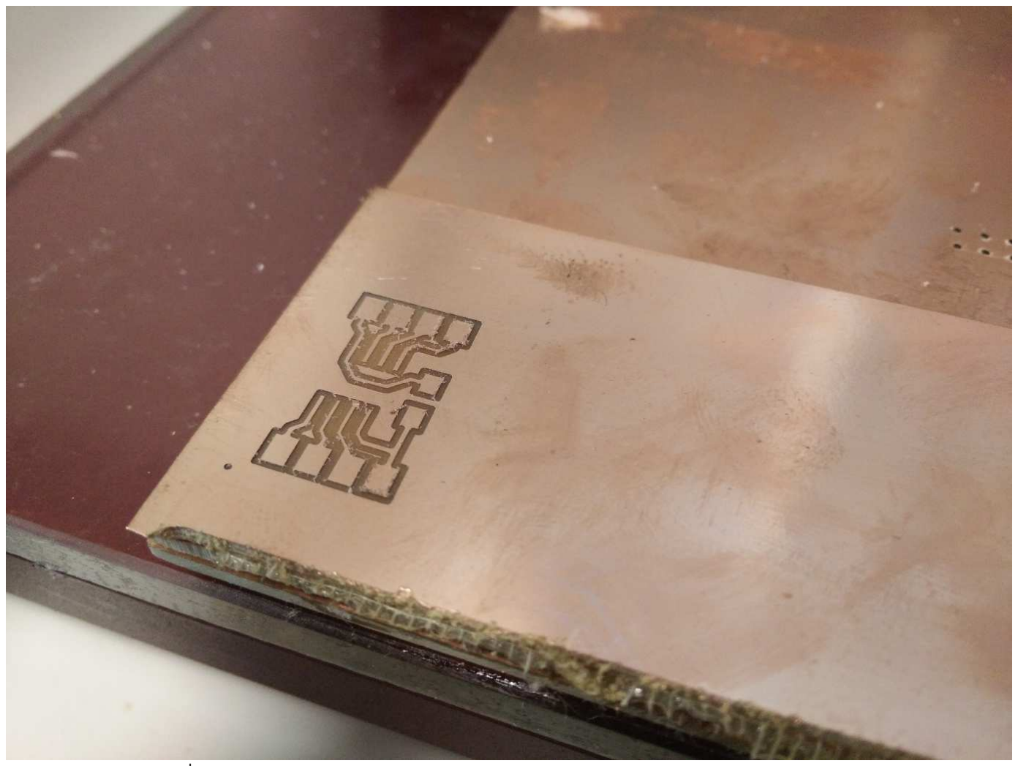
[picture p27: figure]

We can get the 2nd motor setup while the traces are being cut. Switch the motors over, click OK. For the first few holes, keep your hand over the emergency stop button! If the drill doesn’t completely clear the copper between the first two holes be ready to hit stop! This is why we set the Safe Retract Height to 7mm. Our drill bit is extending 2mm below the floating head, and we overdrove the Z height by 1.5mm. The extra 3.5mm is to give us a bit of breathing room.

When the drilling is finished, turn off the vacuum and you should have something that looks like the image below. If you are taking the easy option, you’re now finished with the Denford. Carefully remove the PCB (you might want to use one of the spatulas or even the heat gun if you used the carpet tape).

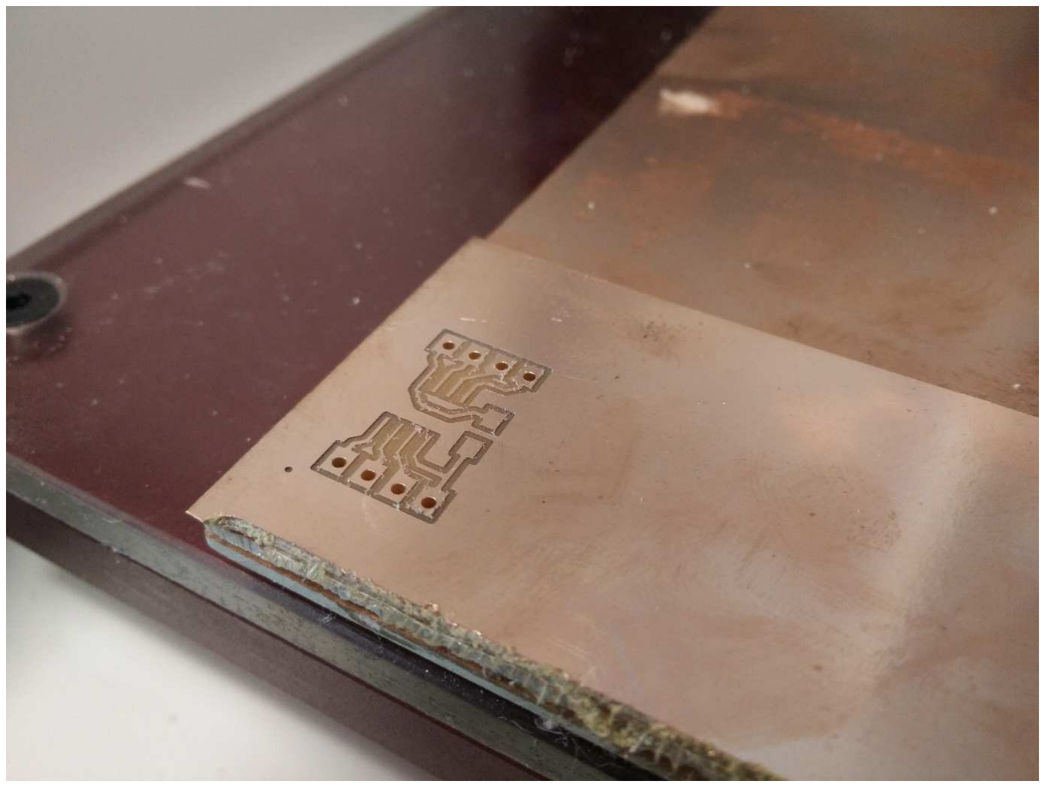
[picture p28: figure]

Hopefully, you now have a lovely PCb ready to be cut out, cleaned up and soldered.

### Cutting Out A Board Cutting Out A Board

Skip ahead to the “Board Cleanup” section if you are getting Graham/Lindsey to cut the circuit out for you using the bandsaw.

To cut out a board, we need to do some manual tweaking of G-Code. To start, import the PCB outline gerber. Don’t make any changes until you get to the toolpath generation. When you get to the toolpath generation, make sure to change the cutter diameter to 1.5mm.

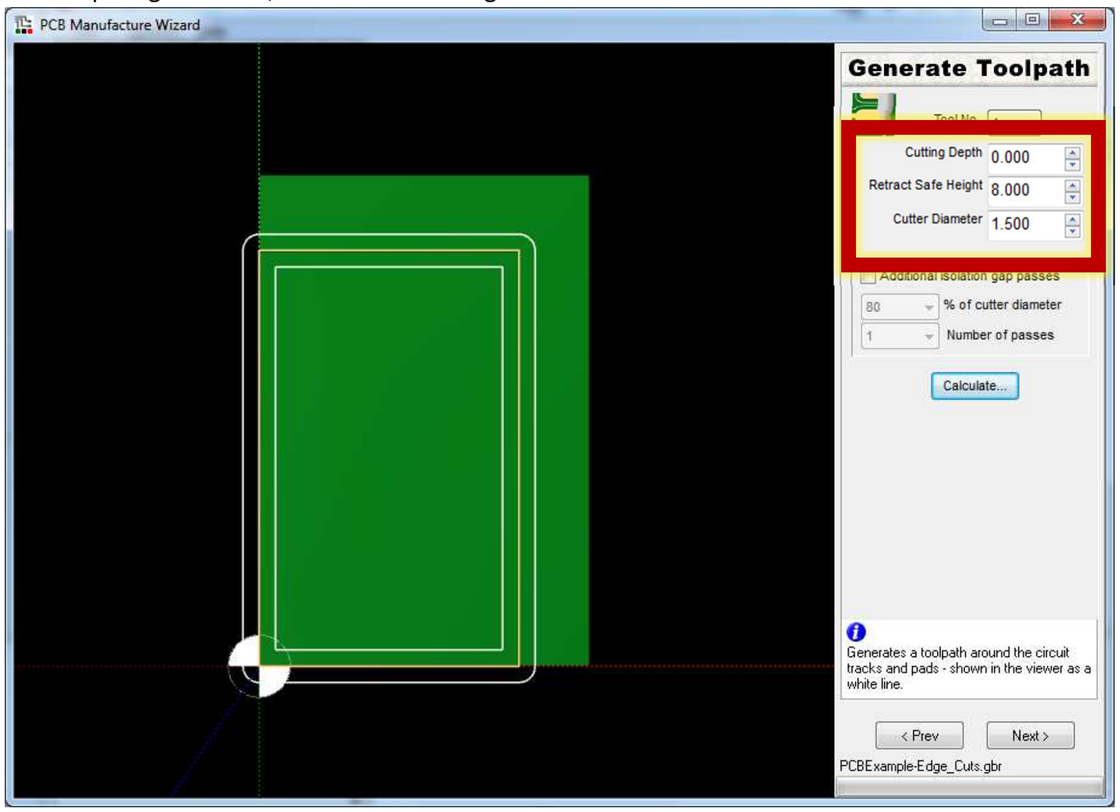
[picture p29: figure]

Notice that if we were to cut this path directly, we would end up with a cut outside AND INSIDE our PCB outline, which will probably destroy our PCB. We would also be trying to cut through the entire PCB in one pass which would probably break the endmill.

For now, click through the rest of the wizard. Your outline will get imported and be placed next to the PCB we just milled. Make sure you know where you saved the .fnc file.

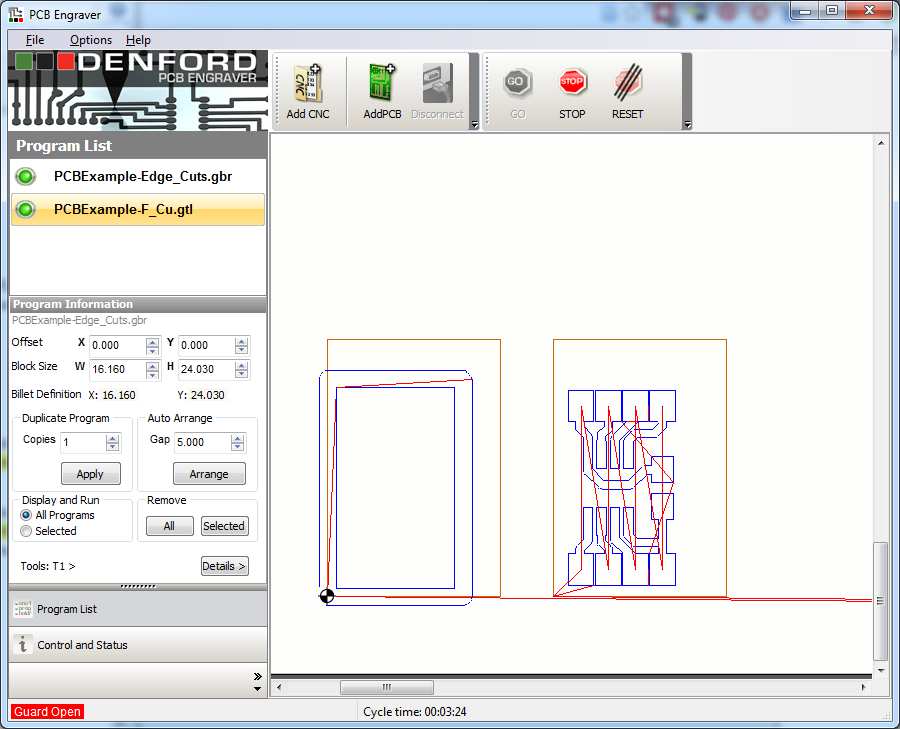
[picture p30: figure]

Click on Program List on the left hand window and right click on your edge cut program (in the above example, mine is called PCBExample-Edge_Cuts.gbr) and delete it. Now, in a text editor (e.g. Notepad) open the .fnc file we just created to cut out the board. You’ll have a file similar to the one shown below.

(Denford Gerber to NC Wizard
(---------------------------
(Filename: PCBExample-Edge_Cuts.gbr (Date: 29/08/2015
(Time: 14:47:18
(Board Side: Component Side
(Track Cutting Depth: 0.000mm
(Track Cutting Tool: T1 Diameter: 1.500mm [TOOLDEF T0101 D1.5000
(Drilling Depth: 2.000mm
(---------------------------
G21
[BILLET X16.160 Y24.030 Z1.600 G90
G91 G28 X0 Y0 Z0
M05
G90 M6 T1
M03 S23000
G0X0Y0Z8.000

G1Z8.000F600.000
G0Z8.000
G0X0.800Y19.526
G1Z0.000
X0.800Y19.526
X0.800Y0.794
X11.900Y0.794
X11.900Y19.526
X0.800Y19.526
G0Z8.000
G0X13.500Y20.320
G1Z0.000
X13.500Y20.320
X13.500Y0.000
X13.477Y-0.191
X13.408Y-0.372
X13.299Y-0.530
X13.154Y-0.658
X12.984Y-0.748
X12.796Y-0.794
X12.604Y-0.794
X0.096Y-0.794
X-0.096Y-0.794
X-0.284Y-0.748
X-0.454Y-0.658
X-0.599Y-0.530
X-0.708Y-0.372
X-0.777Y-0.191
X-0.800Y0.000
X-0.800Y20.320
X-0.777Y20.511
X-0.708Y20.692
X-0.599Y20.850
X-0.454Y20.978
X-0.284Y21.068
X-0.096Y21.114
X0.096Y21.114
X12.604Y21.114
X12.796Y21.114
X12.984Y21.068
X13.154Y20.978
X13.299Y20.850
X13.408Y20.692
X13.477Y20.511
X13.500Y20.320
G1Z8.000
M03 S23000
G91 G28 X0 Y0 Z0
M30

This might look complicated at first, but it’s quite easy to spot the part we’re interested in once you get used to it. I’ve highlighted it in the code above. Here’s a quick overview of what the highlighted section of code does:

### 1. G0Z8.000 tells the machine to move the endmill to the safe height of 8mm

2. G0X0.800Y19.526 then tells it to move to the starting position of the first cut.
3. G1Z0.000 drops the endmill to the cutting depth (in this case 0mm).

### 4. The XY commands like X0.800Y19.526 tell the endmill to do an absolute move by a set

distance in each axis.
5. Again, G0Z8.000 causes the endmill to retract to the safe height, ready to move and start the next cut. This

Because our board outline file only produced two cutting paths, it’s pretty easy to tell what code we need to delete in order to remove the cut on the inside of the line. In the example above it’s the code in yellow. If you highlight each block of code between G1Z8.000 commands, typically the shorter of the two blocks will be the inside line, and the longer of the two blocks will be the outside cut we want to actually do.

Go ahead and delete the code highlighted in yellow above and save it as a new .fnc file. To check we got it right, click the Add CNC button and choose the file we just saved. You should see that we have successfully removed the inside cut and just kept the outside one.

We still have a problem though – right now if we tried to do the board online cut, it would try and cut all the way through the board in one pass and break the endmill. To fix this, re-open the .fnc file we just made in text editor.

We already identified the code that cuts the correct shape, and we know that the command G1Z0.000 will control how deep the cut is. So, we can copy and paste the code for the shape, and just adjust the cut depth each time. I like to cut about 0.6mm per pass, and to do a first pass that just hits the copper and no more (it gives a slightly neater edge on the final copper cut). Boards are about 1.6mm thick, so overall I tend to do my cuts as 4 passes: 0mm, -0.6mm, -1.2mm and then -1.9mm to make sure I get all the way through thicker boards. In the end your program will look something like the code below. Note that lines starting with an open bracket are comments in G-Code. I’ve stripped out the XY moves to keep the code smaller here.

(some header code
(1st pass
G0X13.500Y20.320
G1Z0.000
(a bunch of XY moves)
G1Z8.000
(2nd pass
G0X13.500Y20.320
G1Z-0.600
(a bunch of XY moves)
G1Z8.000
(3rd pass
G0X13.500Y20.320
G1Z-1.200
(a bunch of XY moves)
G1Z8.000
(4th pass
G0X13.500Y20.320
G1Z1.900
(a bunch of XY moves)
G1Z8.000

M03 S23000
G91 G28 X0 Y0 Z0
M30

If you want to take a look at an example of an original edge cut file and a fixed one, take a look at the files “PCBExample-Edge_Cuts_original.fnc” and “PCBExample-Edge_Cuts_fixed.fnc”.

If everything went well, you should end up with your fixed edge cut job imported as shown below.

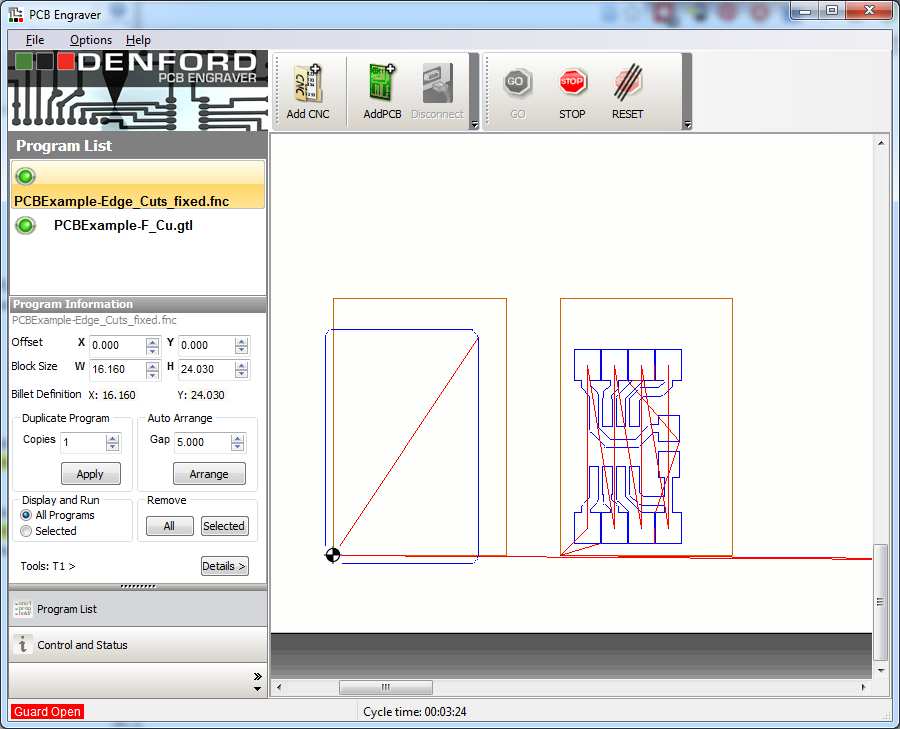
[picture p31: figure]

To align the two jobs, simply select each in turn and make sure that the Offset setting is at 0 for the two jobs. You should end up with the two jobs on top of each other as shown.

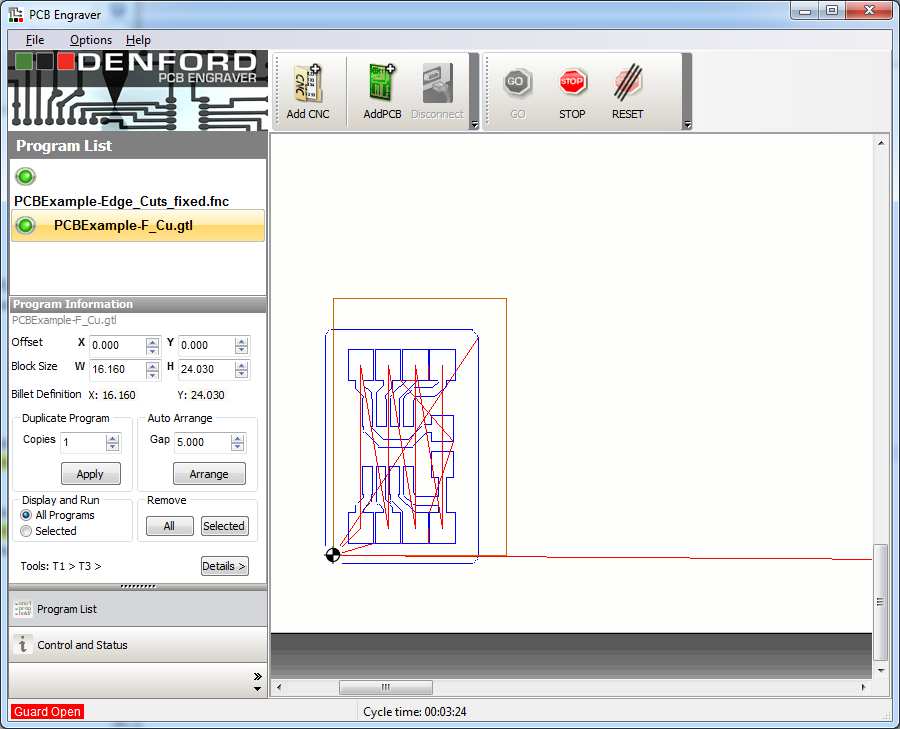
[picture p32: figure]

We’re almost ready to cut! We still need to switch to the 1.5mm endmill and most importantly RESET THE Z ORIGIN.

Because we’re not using the floating head, it’s really important to reset the Z origin. If we don’t, our first pass at a depth of 0mm will actually try and cut all the way through the board! So, jog the machine to the bottom left corner of your pcb, turn on the spindle and then drop the endmill until it is just penetrating the copper and no more. Then, set that height as 0 by clicking the target sign as we did when setting the Z height initially.

The last thing to do is in the Program List tab on the left hand side of the screen, switch the Display and Run option from All Programs to Selected. Make sure you have your edge cut job selected as shown below.

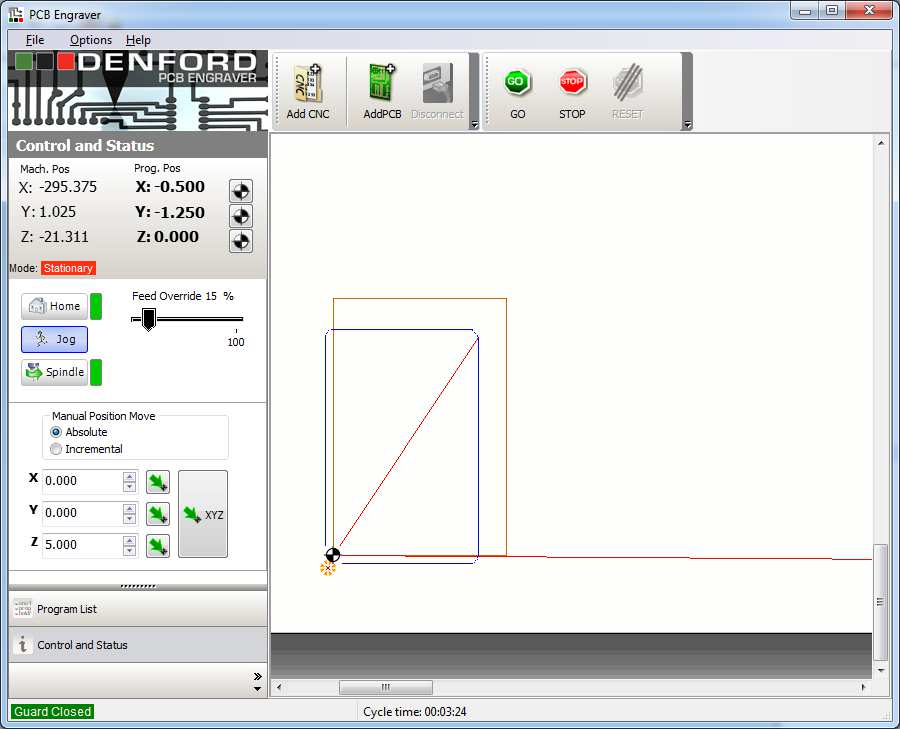
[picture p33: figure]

When you’re ready, turn on the vacuum and hit GO. Keep an eye on the machine to make sure it’s doing what we expect. We hand edited the G-Code so there is a good chance we made mistakes! If it looks like something is wrong, hit the emergency stop.

When the job is finished, you should have one nicely cut out PCB! The next job is to clean up the PCB, ready for soldering.

### Cleaning the PCB Cleaning the PCB

Depending on how new the endmill was, our PCB might have a lot of burrs (sticking up bits of copper that haven’t quite detached from the traces). I was using a new endmill when I wrote this so the burring on the traces wasn’t minimal. This is what my board looked like before I removed it from the engraver.

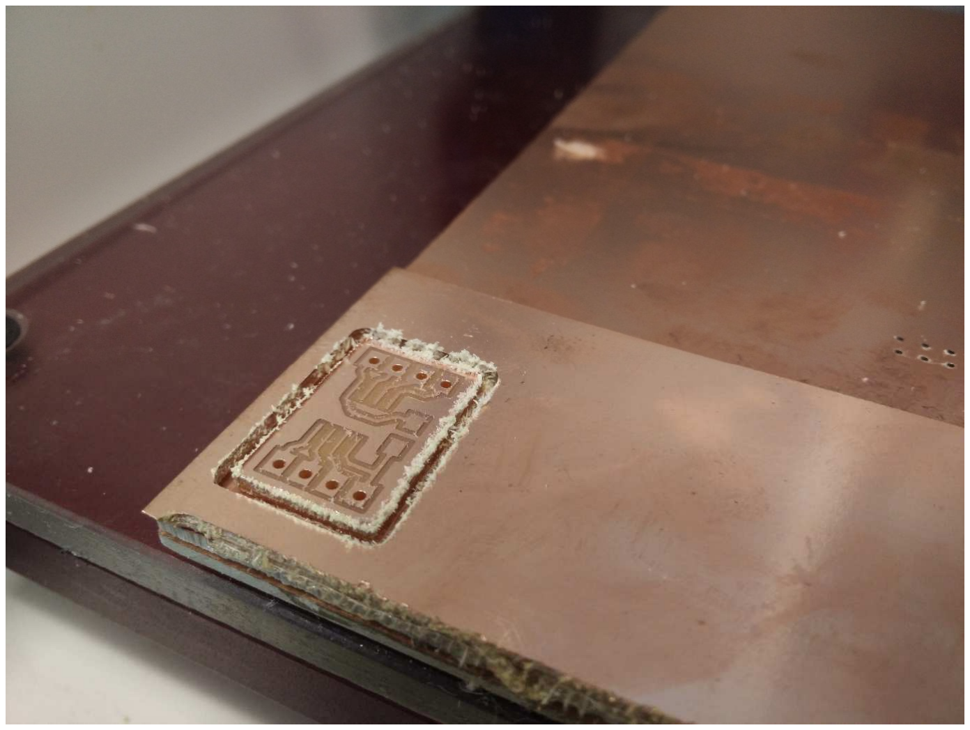
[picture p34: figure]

You can see little flecks of copper around the traces, and what looks like a mess around the board outline (it’s actually just from the double sided tape). I used the metal spatula thing for getting 3D prints off the 3D printer.

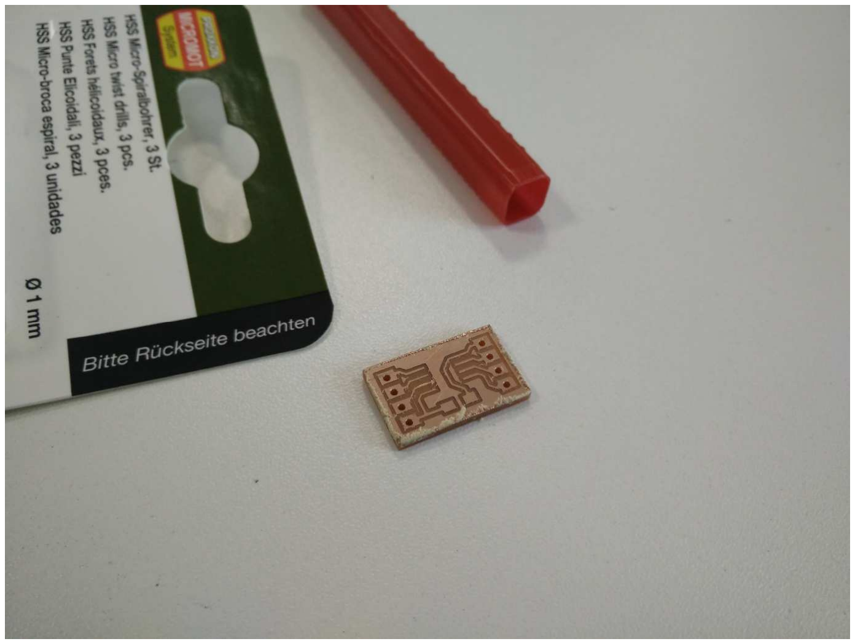
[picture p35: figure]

I then use the flat edge of the spatula to scrape down the edges of the board to remove the worst of the burrs and stuck tape, and then gently draw it across the top surface of the PCB to remove any big burs on the traces. If you were unfortunate enough to be using a really old or damaged endmill, you might even want to use some high-grit wet sandpaper to clean up the top copper. It’s also worth doing a good visual inspection to make sure all your traces are properly cleared. You can use a craft knife to clean up any dodgy looking sections.

The picture below shows an example of the same board cut with an old endmill (top) and a brand new endmill (bottom).

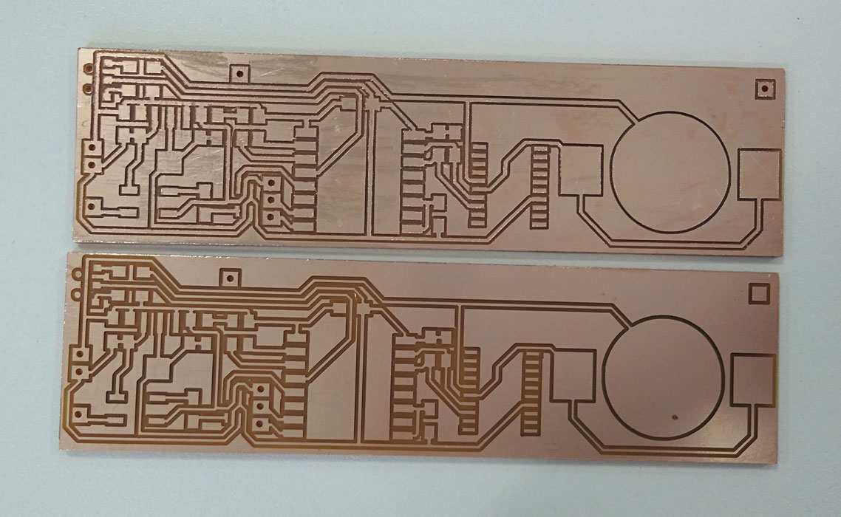
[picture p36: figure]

The top board was using an old bit and had a LOT of burrs. It would have needed a significant amount of work to clean it up. In comparison, the bottom board was cut using a new endmill. It needed almost no post processing at all, and has a super crisp cut.

It's pretty hard to know how a 0.4mm endmill is fairing just by looking at it. I think the easiest way to spot a mill at the end of it's life is based on:

- Track width vs clearance width: I use 0.4mm tracks as a standard, and a new 0.4mm bit

should give a clearance of 0.4mm. As the mill wears out, it's cutting width decreases. On the bottom board, you can tell that the traces and cuts are about the same width. On the top board, the traces are significantly wider.
- Burrs: Although some burrs are to be expected, if you feel like you would have to clean up a

lot of traces with a craft knife then there is a good chance the cutter is past it (or you have your settings totally wrong!).

Once you’re happy, go wash the board in hot soapy water and give it a good scrub with an old toothbrush. This helps clear out any little bits of copper caught between traces, and removes the oils from your fingers. If you don’t wash the board, the oil from your skin reacts with the copper over time. This makes the copper very difficult to solder on, and can even cause so much damage that eventually traces get worn away. Just take a look at the sacrificial copper in the machine – you can usually see dark fingerprint marks all over it!

And that, finally, is us done! Go solder your masterpiece!

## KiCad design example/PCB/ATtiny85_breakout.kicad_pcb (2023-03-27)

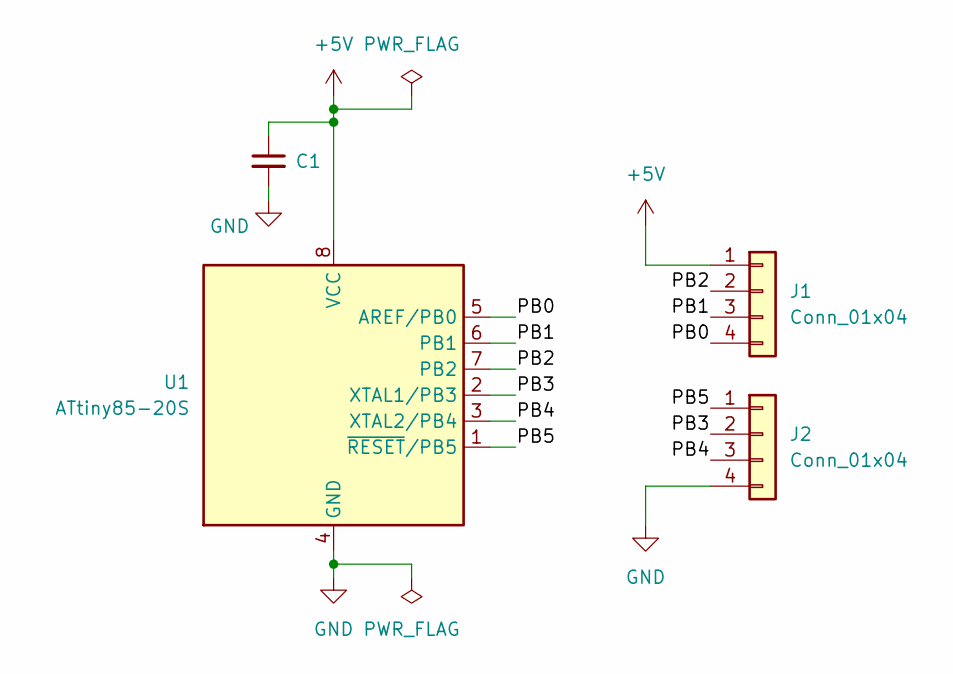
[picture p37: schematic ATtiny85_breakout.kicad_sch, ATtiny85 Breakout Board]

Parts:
C1: C_Small; C_1206_3216Metric_Pad1.33x1.80mm_HandSolder
J1, J2: Conn_01x04; PinHeader_1x04_P2.54mm_Vertical
U1: ATtiny85-20S; SOIC-8W_5.3x5.3mm_P1.27mm

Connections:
+5V: C1.1, J1.1, U1.8 (VCC)
/PB0: J1.4, U1.5 (AREF/PB0)
/PB1: J1.3, U1.6 (PB1)
/PB2: J1.2, U1.7 (PB2)
/PB3: J2.2, U1.2 (XTAL1/PB3)
/PB4: J2.3, U1.3 (XTAL2/PB4)
/PB5: J2.1, U1.1 (~RESET/PB5)
GND: C1.2, J2.4, U1.4 (GND)

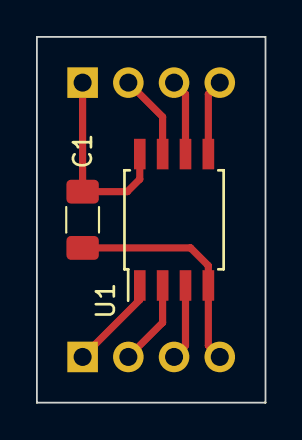
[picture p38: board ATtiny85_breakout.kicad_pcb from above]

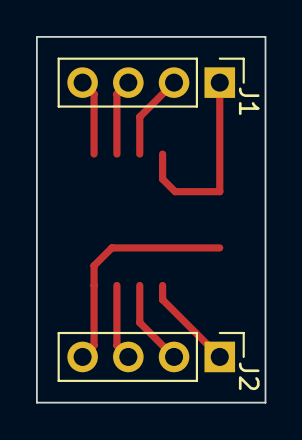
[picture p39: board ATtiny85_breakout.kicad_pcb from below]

Board: 2 copper layers, 12.7 x 20.3 mm, 4 parts (2 on the bottom side), 8 nets.

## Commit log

2015-08-29 First commit of KiCAD project files
    [PCBExample.kicad_pcb, PCBExample.sch]
2015-08-29 Adding gerbers
    [PCBExample-Edge_Cuts.gbr, PCBExample-F_Cu.gtl]
2015-08-30 Adding original and fixed drill files, generated trace mill .fnc and generated and original cutting fnc
    [PCBExample_fixed.drl, PCBExample_original.drl]
2018-08-14 Update tomake it clearer that setting the Z height should be done with a drill bit set at 2 mm depth
2023-03-27 Remove old tutorial example files
    I'll update to KiCAD 6.0 and just use default included footprints.
    [PCBExample.kicad_pcb, PCBExample.sch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]
2023-03-27 Add KiCAD 6.0 example PCB
    This is just a remake of the original example PCB, but uses only footprints found in the default KiCAD 6.0 install.
    [ATtiny85_breakout.kicad_pcb, ATtiny85_breakout.kicad_sch]
2023-03-27 Add example gerber output
    [ATtiny85_breakout-Edge_Cuts.gbr, ATtiny85_breakout-F_Cu.gbr, ATtiny85_breakout.drl]
2023-03-27 Add pcb2gcode settings file for Denford
2023-03-27 Add example pcb2gcode output
2023-04-04 Fix caps on folder name
    [ATtiny85_breakout.kicad_pcb, ATtiny85_breakout.kicad_sch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]
2023-04-05 Add link to KiCAD getting started tutorial
    Also switched to relative doc links.
    A few minor corrections.
2023-04-05 Add use case recommendations
2023-04-05 Gerber generation intro
2023-06-06 Add no silkscreen note
2023-06-06 Add KiCAD gerber export settings section
2023-06-06 Inital pcb2gcode section
